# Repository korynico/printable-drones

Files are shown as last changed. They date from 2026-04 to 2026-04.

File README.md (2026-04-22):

# 3D printable drone frames and parts

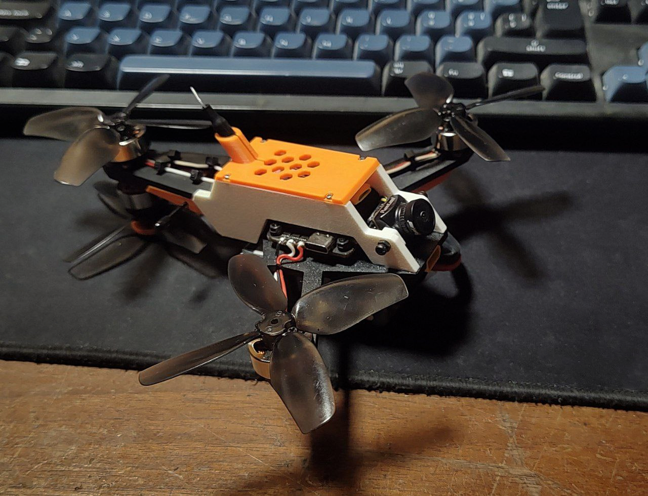
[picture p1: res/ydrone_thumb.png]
Small 3D printed Y4 quadcopter


Hiii! This repository contains printable models and various info for my 3D printed drone projects. These models are designed to be very easy to print (with flat, no support PLA parts where possible) while staying stiff and dusable enough to handle crashes, allow proper-ish tuning, and not commit spontaneous self-disassembly.

## General info and build tips

### Disclaimer

I do not assume any responsibility for damages or injuries from your use of (or misuse of (or taking inspiration from)) these projects. Be careful, copters bite regardless of size. These ones use homemade plastic parts, building them is easy but leaves a lot of room for error and oversight - including on my side. These are my hobby projects, not certified bombproof designs.

Feel free to share, use, modify or remix. Do not sell project sources, builds, prints, or derivative works. Please give credit and link to the original source.

Take care and have fun!

### Purchasing from AliExpress

AliExpress text based search is barely usable and makes it very difficult to find the right item or compare prices between listings for the same product. Your best option is to use the site's image based search, especially when comparing prices. I have included pictures for most parts you can directly paste into AliExpress's image search to find matching listings.

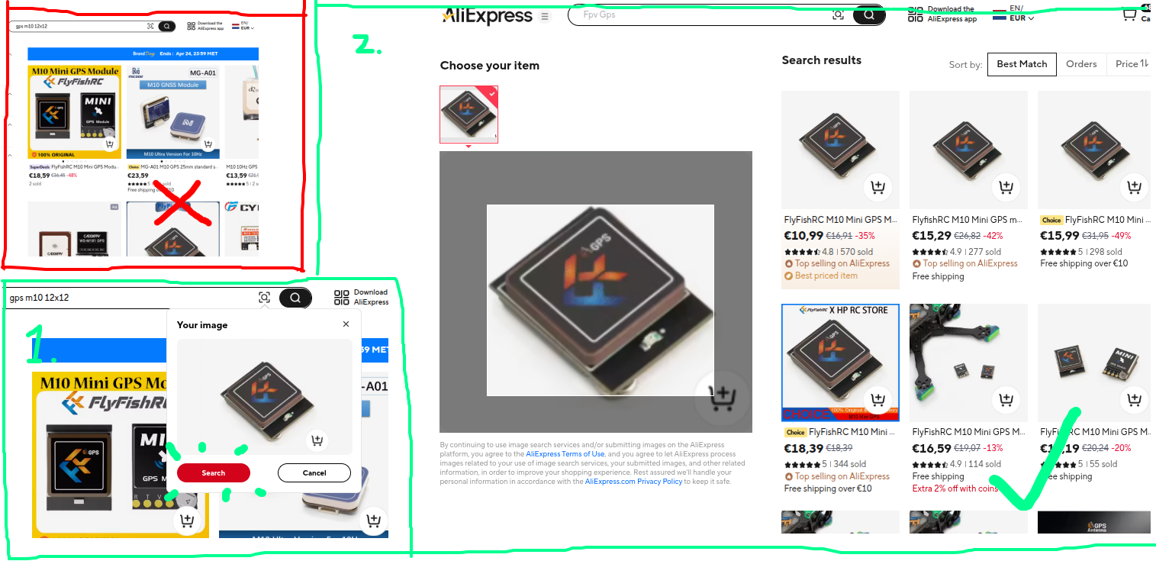
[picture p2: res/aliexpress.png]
AliExpress image search demo


# 3" Y4 Quad (made with illegally cheap motors)

I found some ~~cursed~~ cheap motors on AliExpress (about 0.75$ each, similar to the ones that are commonly used in cheap Chinese camera drones and DJI lookalikes) and felt like making a 3D printed quad with them, and some spare parts. I decided to go with a Y4 configuration, mainly because it looks cool.

The design is not perfect - the FC can't be easily removed after assembly (so finish soldering first and only *then* glue the frame) and there are many areas left for improvement, but I'm overall happy with the design.

Parts used:
- **AIO FC** (30.5x30.5 mounting, 4S compatible)
  - eg. SpeedyBee F405 AIO; or GEPRC TAKER G4 AIO (I strongly recommend against buying GEP)
- **HGLRC Zeus nano**  (w/ monopole antenna)
- **ELRS nano receiver** (w/ dipole antenna)
- **Camera** (w=14mm)
- **Tattu 850mAh 4S 95C Lipo HV Battery**
- **20x M1.7 screws (!)** (*18x h=5mm* for the props and motors, 2x h=10mm for the inverted prop)
- **7x small thread forming screws** *d=1.2mm h=5mm*, for the reverse mounting plate)
- **XT30 female connector**
- **Motors and matching props**, *see below*
- The 3D printed parts of course
- Small cable ties
- Tons of super glue

> [!NOTE]
> ### Printing
>
> **Print parts from PLA.** Not PETG, not PA, not other materials unless you really know what you're doing.
>
> **Lay parts flat, use 100% infill, and an alternating/rectilinear infill and surface pattern.**
> 
> **Use liquid cyanoacrylate / super glue** generously. Glue all touching surfaces, except for the cover plate and inverse motor mounting plate. Those should be held in place with screws only.
>
> The **battery holder should be printed from TPU**. Position it upright and use supports. 

> [!NOTE]
> ### Motors, props
>
> **The motors use M1.7 screws**, and have unusual thread spacing and keying on the bell. They are - afaik - only compatible with made to match propellers (or interference fit "no screw" props; however no such props (should) really exist in a 3" format.)
>
> Matching propellers are very cheap but also break easily. Make sure to pick up a lot of them. A 20x pack sould be in the <$10 range.
>
> Some of my pictures show motors without an exposed shaft. **Make sure to buy motors with exposed shafts**. This is required for inverse-mounting the propeller. You can use the included images to find the correct parts.
>
> Use a spacer when inverse mounting the bottom tail propeller.

> [!TIP]
> Unlike carbon composite, cracked and snapped PLA parts can be repaired with super glue. *Use a lot of glue and make sure the surfaces are properly covered and in full contact*.

## Build steps

I haven't documented the build step-by-step, but the craft is very simple to assemble. The steps are briefly as follows:
1. Print all parts (found in `models/01_y4mini/`). File names starting with `b_`, `w_`, and `c_` indicate black, white, and colored parts in my build. `tpu_` should be printed from 90-95A TPU.
2. Fasten the AIO (along with the battery holder) to the main plate, and mount the motors.
3. Solder leads to the VTX and receiver, then pass them through the holes in the top plate.
4. Loosely assemble the frame (do not glue yet), then trim all leads to the correct length and solder them to the AIO. Solder the battery connector to the AIO.
5. Fasten the VTX and receiver to the top plate. Use cable ties for the receiver.
6. Glue the frame pieces together (except the top cover and inverse motor mounting plate). Thoroughly glue all adjacent surfaces.
7. Secure the motor leads to the frame with cable ties. Snap the receiver antenna into the slots below the tail.
8. Secure the top cover and motor mounting plate to the frame with screws.

### WIPs

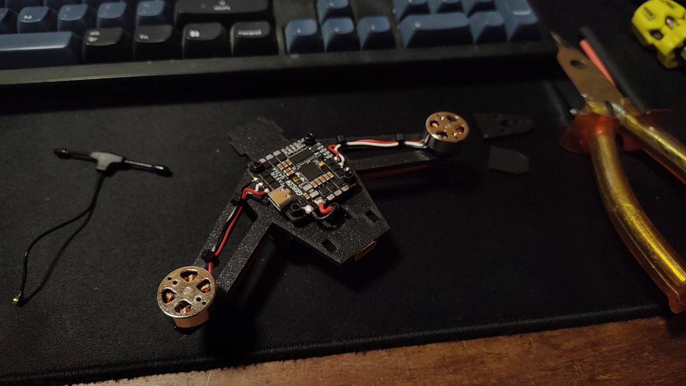
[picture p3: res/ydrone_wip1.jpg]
Y4 quadcopter work in progress, base plate


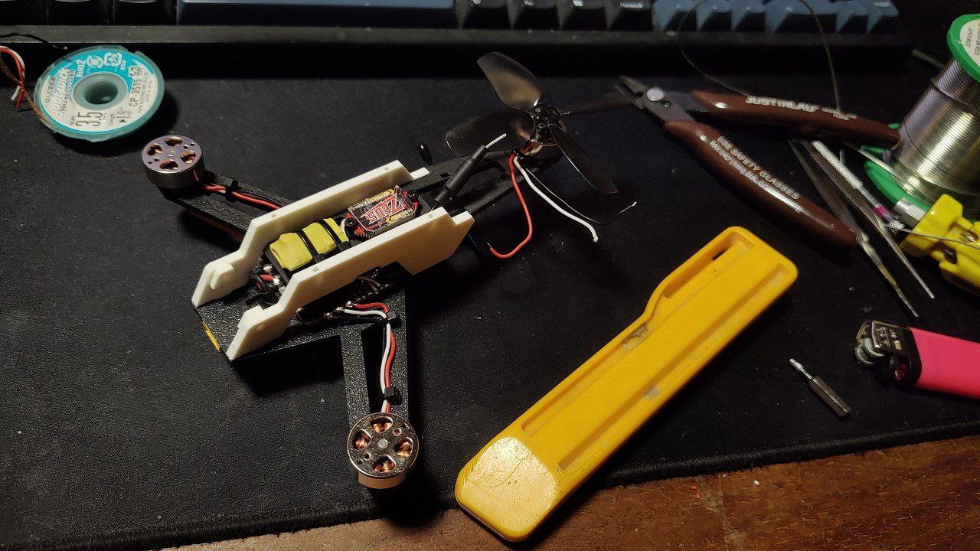
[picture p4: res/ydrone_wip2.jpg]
Y4 quadcopter work in progress, top plate and side panels assembled


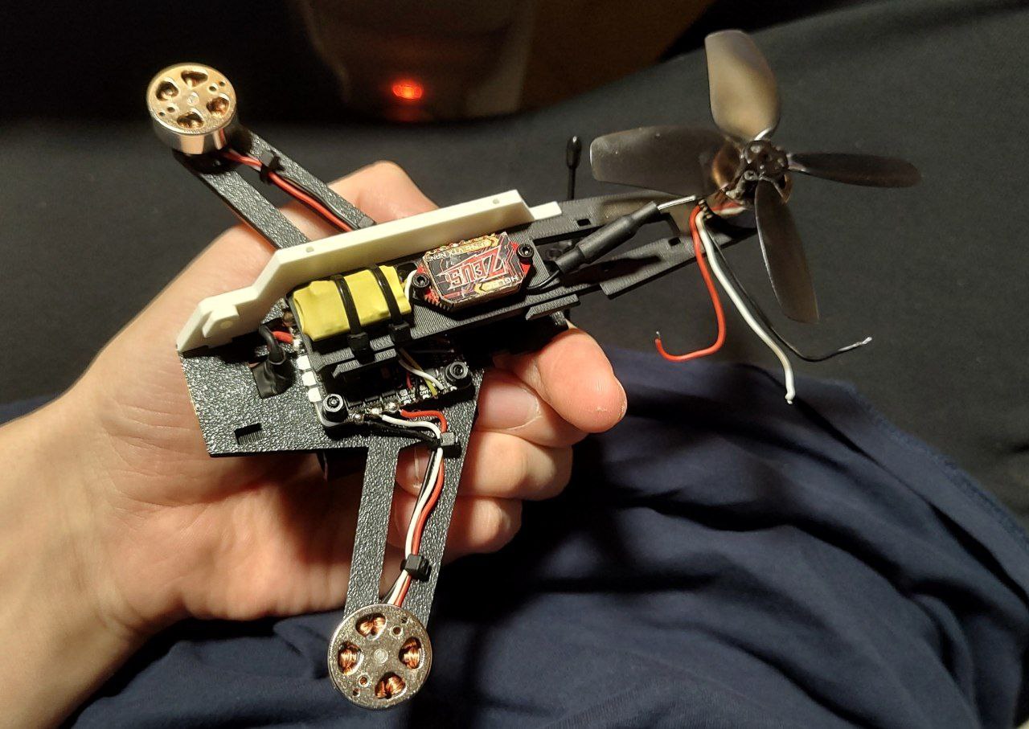
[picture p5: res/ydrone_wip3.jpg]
Y4 quadcopter work in progress, top plate and side panels assembled, side panel missing


### 3D / exploded view

> [!NOTE]
> Parts in the 3D views may slightly differ from the current up to date models. Assembly and mounting *should be* unchanged.

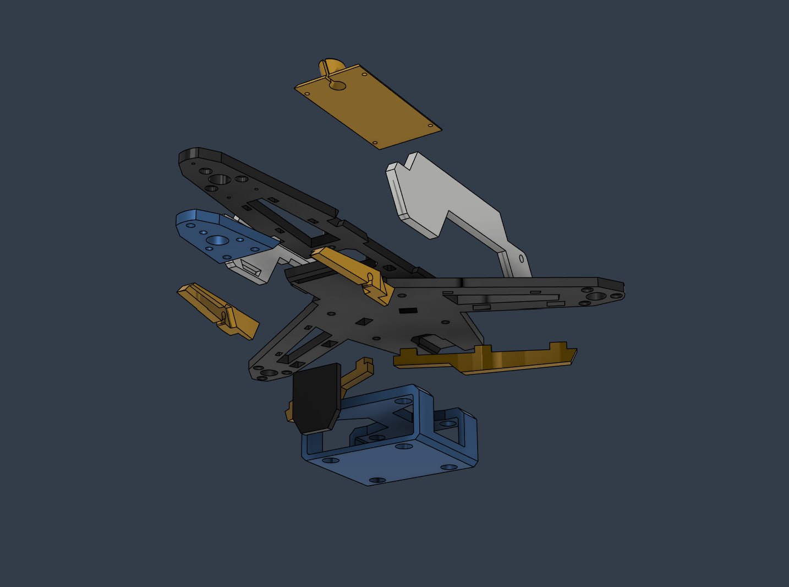
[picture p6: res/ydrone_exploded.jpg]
Y4 quadcopter parts, exploded view


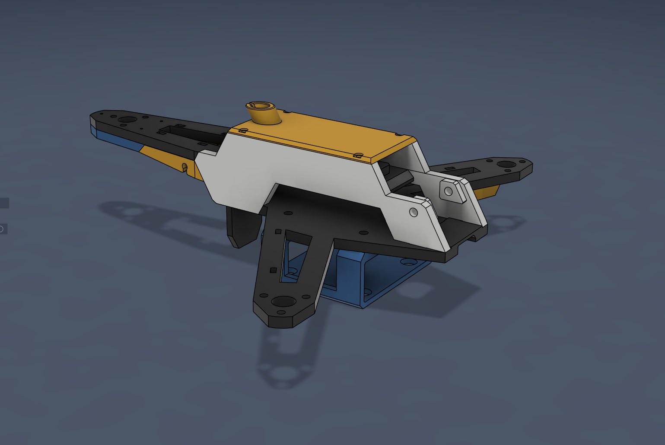
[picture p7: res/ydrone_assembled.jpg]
Y4 quadcopter parts, assembled view


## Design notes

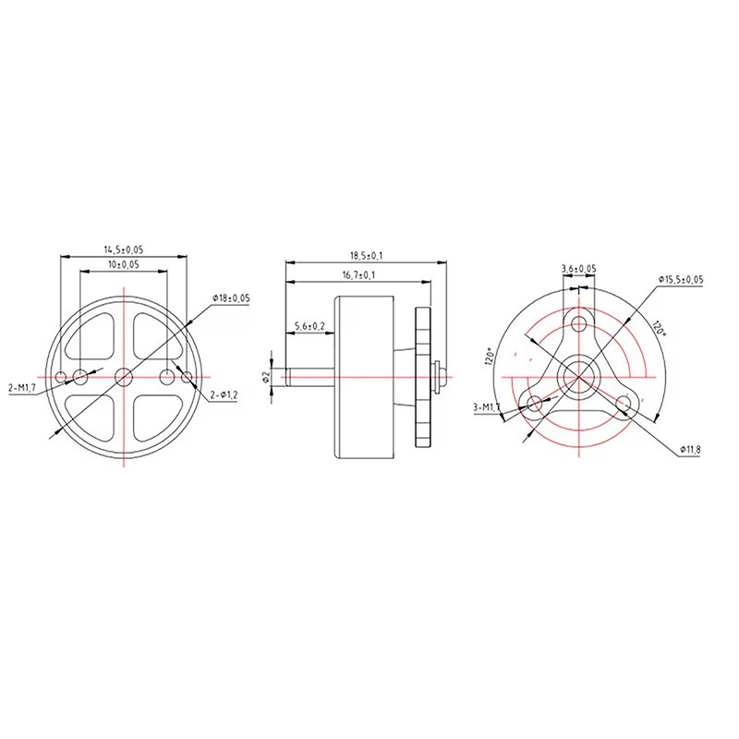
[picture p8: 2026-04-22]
res/aliexpress/y4_motors_1.jpg

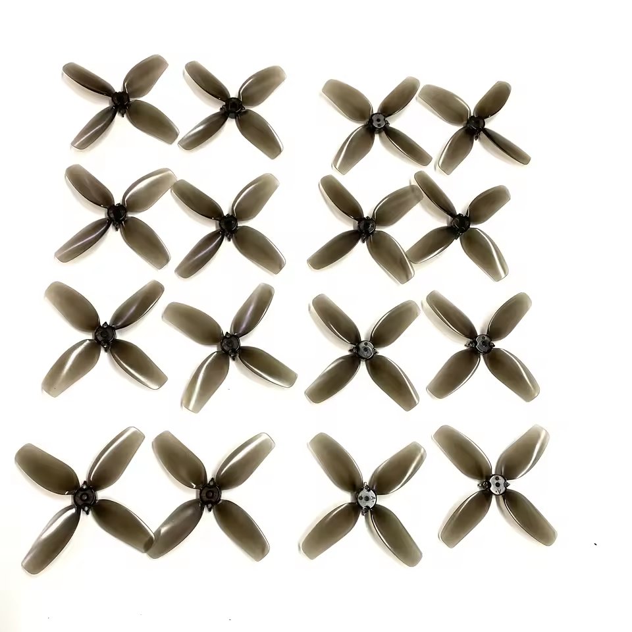
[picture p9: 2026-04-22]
res/aliexpress/y4_props_1.jpg

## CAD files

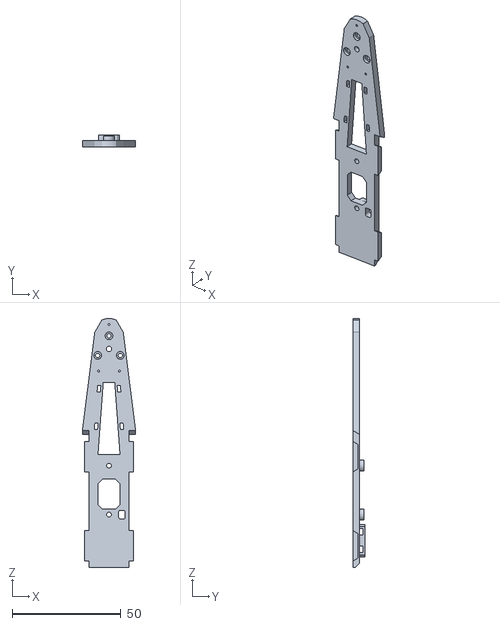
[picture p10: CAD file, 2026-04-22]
models/01_y4mini/b_topplate.stl
24.5 x 5.50 x 114.5

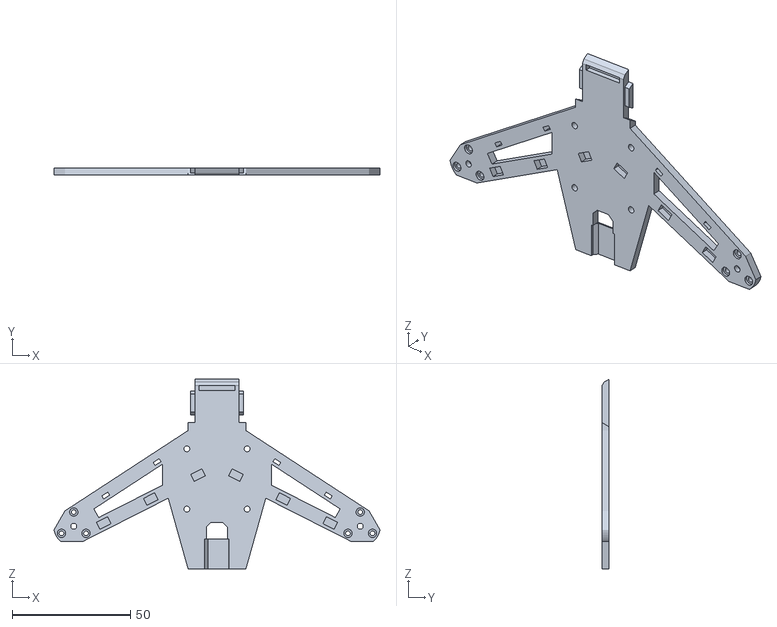
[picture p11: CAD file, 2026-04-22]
models/01_y4mini/b_baseplate.stl
138.0 x 3.00 x 80.2

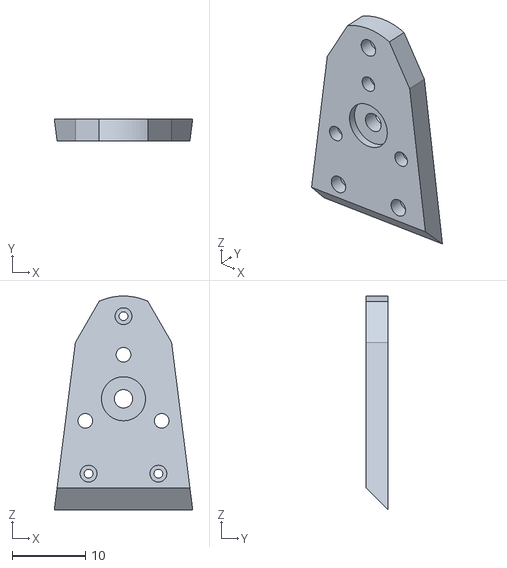
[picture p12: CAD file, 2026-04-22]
models/01_y4mini/b_motorplate.stl
18.9 x 3.00 x 29.1

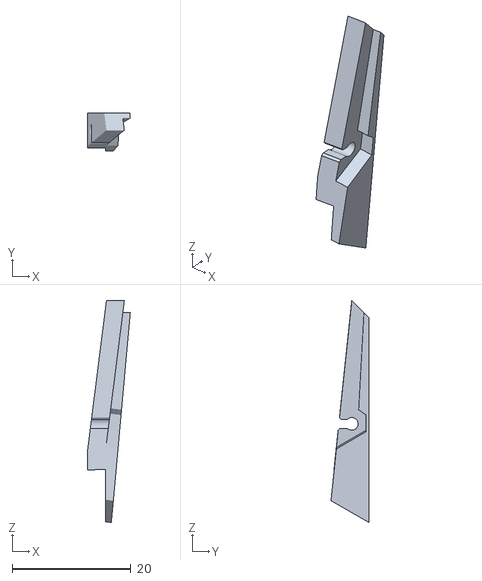
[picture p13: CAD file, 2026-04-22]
models/01_y4mini/c_antennaholder_l.stl
7.19 x 6.38 x 37.4

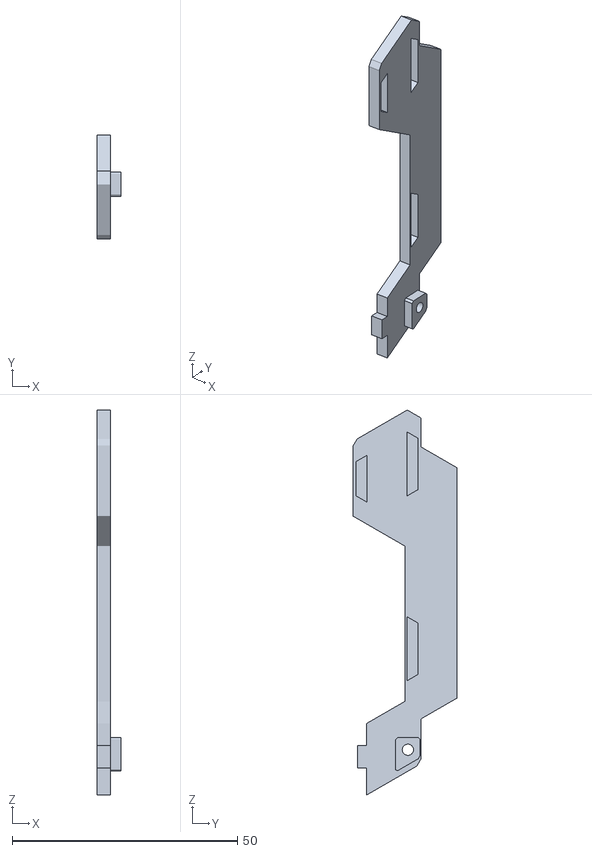
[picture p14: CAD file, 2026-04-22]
models/01_y4mini/w_sideplate_l.stl
5.26 x 23.0 x 85.4

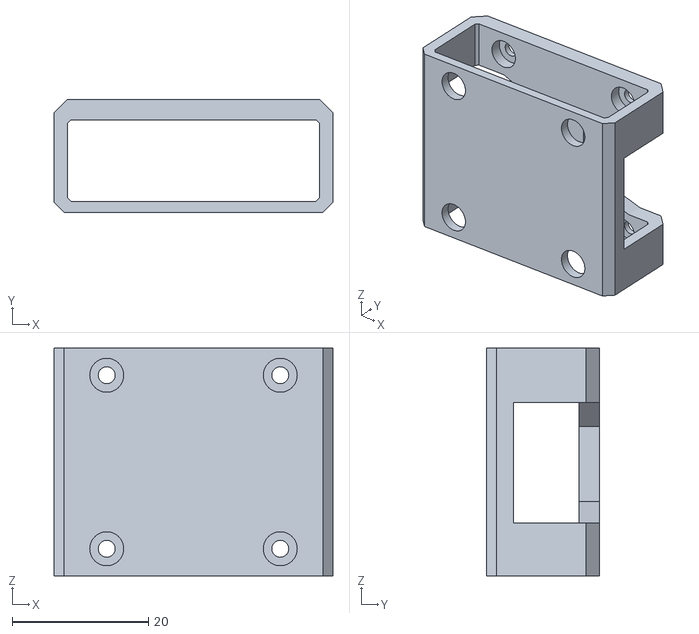
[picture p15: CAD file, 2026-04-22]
models/01_y4mini/tpu_batteryholder.stl
41.0 x 16.6 x 33.5

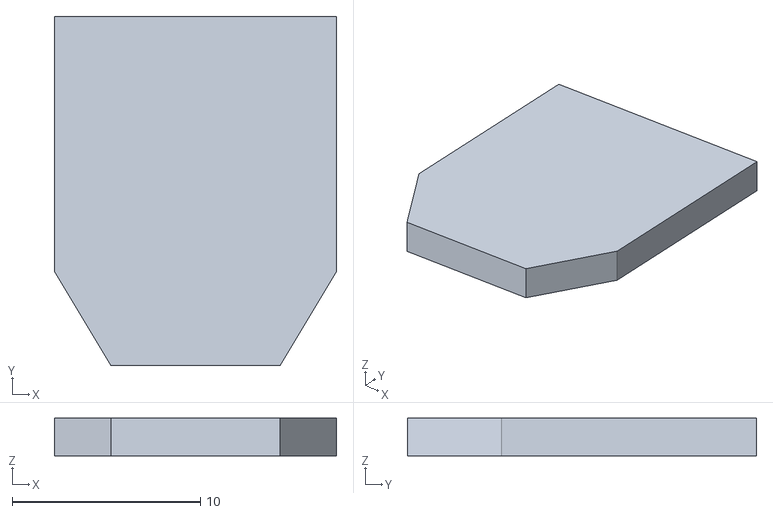
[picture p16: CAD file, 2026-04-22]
models/01_y4mini/b_battery_bumper.stl
15.0 x 18.5 x 2.00

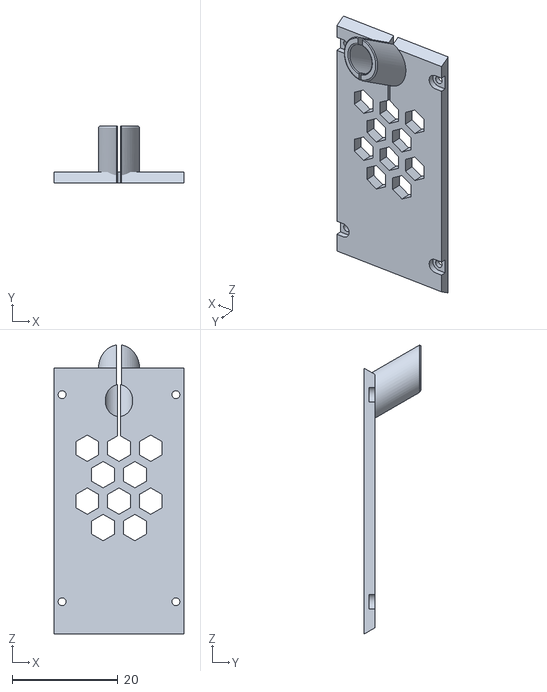
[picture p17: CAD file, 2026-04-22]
models/01_y4mini/c_top_cover.stl
24.5 x 10.7 x 54.7

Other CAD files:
models/01_y4mini/c_antennaholder_r.stl
models/01_y4mini/w_sideplate_r.stl

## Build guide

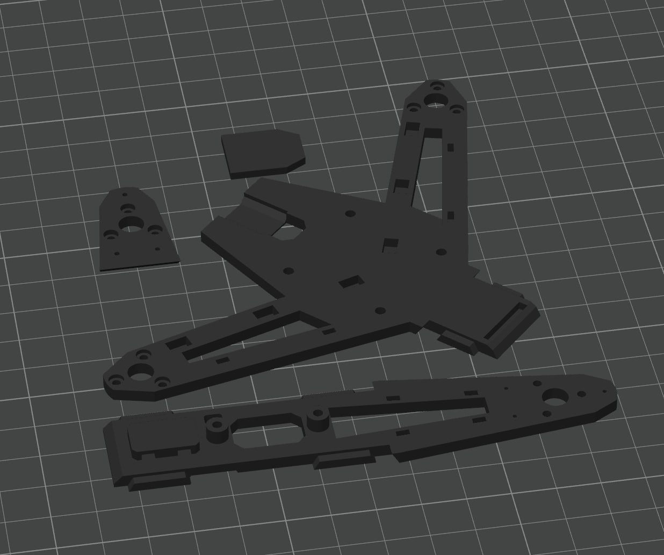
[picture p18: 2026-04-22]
res/ydrone_print1.jpg

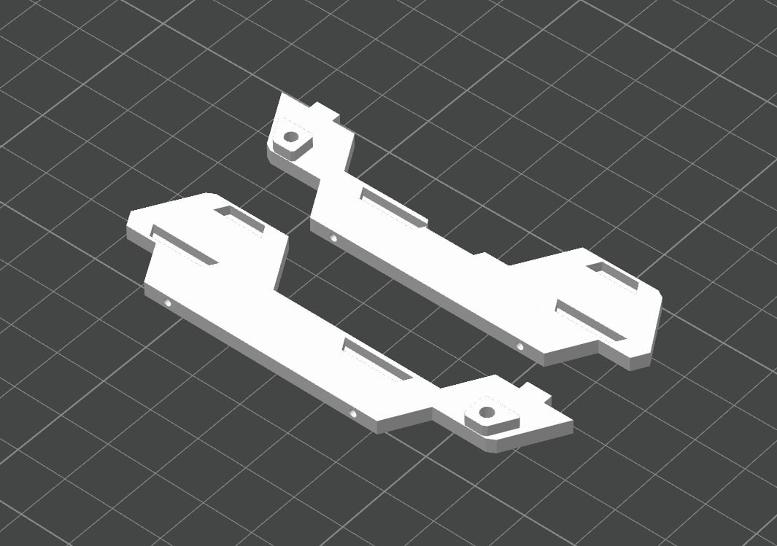
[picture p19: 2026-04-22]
res/ydrone_print3.jpg

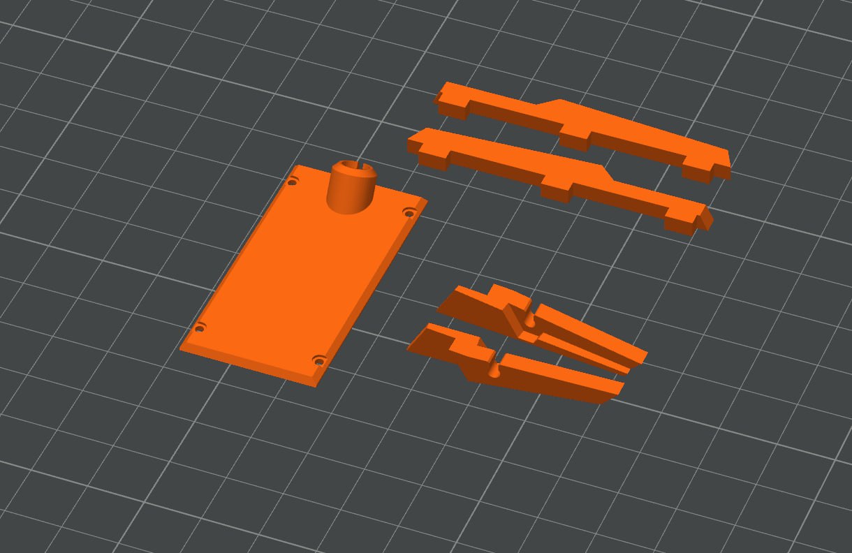
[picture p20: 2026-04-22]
res/ydrone_print2.jpg
